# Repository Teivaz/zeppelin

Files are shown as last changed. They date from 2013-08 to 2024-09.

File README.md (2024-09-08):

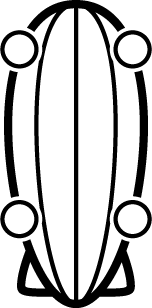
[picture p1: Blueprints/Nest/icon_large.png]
# Zeppelin 

### Airship project with all electrical circuits, PCBs, blueprints, software sources and calculations

### Intended result
First version of this zeppelin should be able to keep itself up in the sky for a decent amount of time. It will be controled remotely (probably via iphone). Total length of airship 168.13cm. Volume 0.46 m3.
In the end it should look like this:    
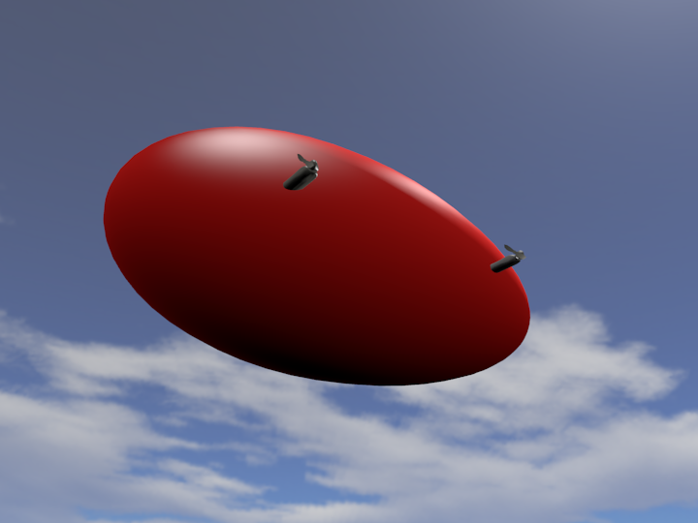
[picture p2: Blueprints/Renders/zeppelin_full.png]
zeppelin in all its glory


### Progress
 - [X] Calculate the overall size, mass, and lifting force of the aerostat
 - [X] Create patterns for aerostat
 - [X] Create electrical schemas
 - [X] Design software architecture
 - [ ] Create and debug airship's software
 - [ ] Create software for controlling unit
 - [ ] Trace PCBs and make all PCBs
 - [ ] Assemble aerostat
 - [ ] Field tests

### Calculations
Here is the [link](https://docs.google.com/spreadsheets/d/1KFVUaK0Eav1PAXg2VrwWtU-BHmDxbaWGcJfdvVmI2J4/edit?usp=sharing) to spreadsheet with calculation I made for the lifting force and mass of the airship 

### Mechanics
Most parts used here were thoroughly measured and calculated. Like these cases for motors and servos (feather module)   
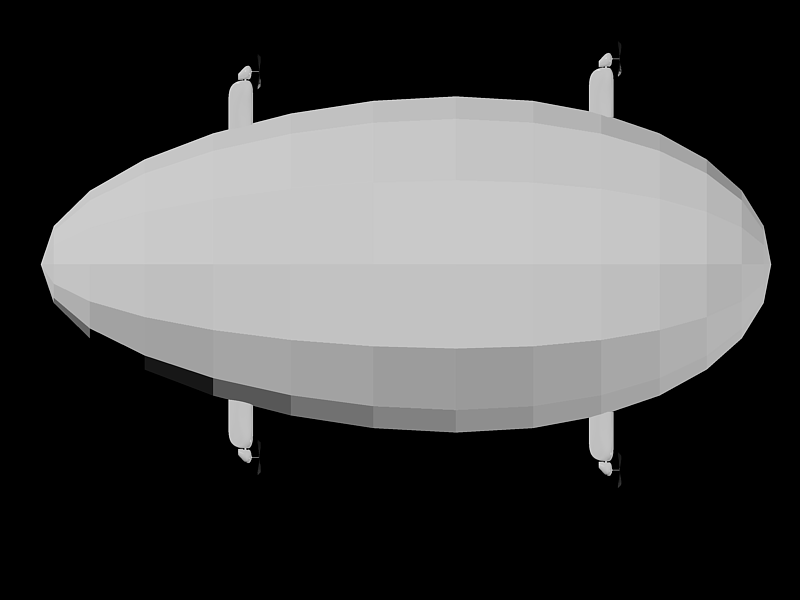
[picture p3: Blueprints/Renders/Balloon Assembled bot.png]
preview
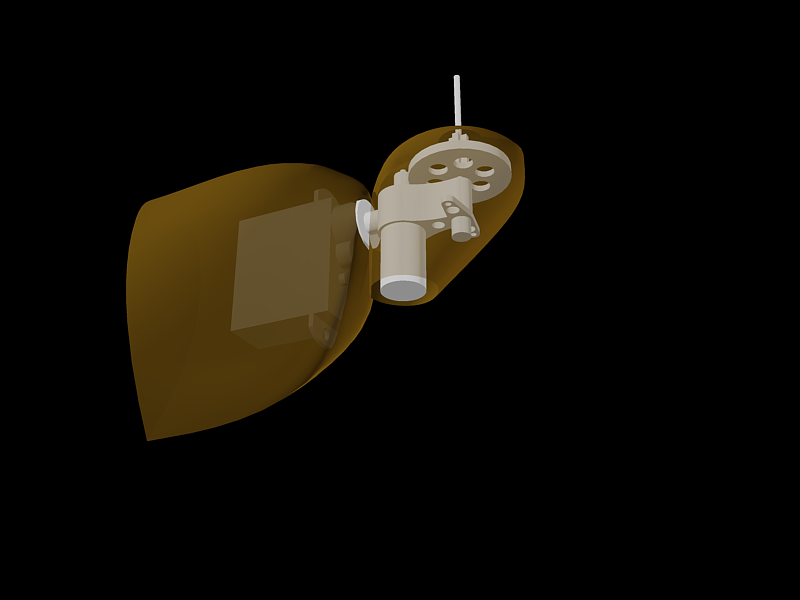
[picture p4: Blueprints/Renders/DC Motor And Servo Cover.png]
feather


### Electronic schematics and PCBs
Well there's not much to say about schematics despite the fact that I'm using ST microcontroller stm32l011f4 and transmitting modules nRF24013. It is designed and traced with [EAGLE](https://www.autodesk.com/products/eagle/overview).

### Software
I am using smt32l011 and the IDE is [VS Code](https://code.visualstudio.com). The language is C with HAL library.

### Version 1.0 considerations
 * Feather MCU should use internal PWM channels directly. This will simplify code and increase working frequency.
 * Feather should use a motor driver that does not short circuit when in low phase of the PWM.
 * Consider using 8 bit controller for the Feather module.

### Further plans
 * Second version will be able to carry a camera.
 * Third version will automatically keep position, folow the route or target.

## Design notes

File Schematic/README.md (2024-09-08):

# Change log

## Version 1.1
Status: In development
Changes:
 - [Keel] Added power regulator.
 - [Keel] Measuring Bat0 through divider.
 - [Feather] Changed pinout for PWM.

## Version 1.0.1
Status: Upgraded from v1.0.0
Changes:
 - [Keel] Replaced vertical connectors with horizontal (fixed connector pin numbers).
 - [Keel] Fixed LED polarity.
 - [Keel] Changed voltage divider resistor.
 - [Keel] Flipped the power switch.

## Version 1.0.0
Status: Manufactured

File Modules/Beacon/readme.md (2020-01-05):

# The Beacon module

This module is used only for testing purposes.

Every second the beacon tramsmits data that should be picked up by the device.

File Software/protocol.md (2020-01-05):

This document describes the communication protocol for the Zeppelin project.

Project URL: https://github.com/Teivaz/zeppelin
Author: Teivaz
Date: 4.01.2020
Version: 1.0

# Purpose
The communication protocol is used to for commands and data transmition between different parts of the Zeppelin.

# Adopting
This communication protocol is adopted by all parts of the system. Certain parts may not support all of the commands but the package structure should always be supported.

# Architecture
The protocol assumes single master and multiple slave devices.

# Package structure

```
|  Hdr  |  Adr  |  Len  |  RId  |  Cmd  |  Pld  |  CRC  |
|  0x55 |  1B   |  1B   |  1B   |  1B   |  ...  |  1B   |
```

The **Hdr** (Header) field. Size: 1 byte. The very first byte of every package starts with a **Hdr** field which is always `0x55` (`0b01010101`).
The **Adr** (Address) field. Size: 1 byte. Compatible with I2C 7 bit address. The MS bit is reserved and should always be 0.
The **Len** (Length) field. Size: 1 byte. Type: `uint8_t`. The length of the rest of the package including its **CRC** byte.
The **RId** (Request/Response Id) field. Size: 1 byte. Type: `uint8_t`. The unique id of the request that will be repeated by the response. Can be 0.
The **Cmd** (Command) of size 1 byte. Full list of commands is in the *Commands* section.
The **Pld** (Payload) field. Size: 0-26 bytes.
The **CRC** field. The (polynomial 0x07, initial value 0x00) CRC-8 value of the whole package (excluding this field).

# Version
The protocol version is `0bMMMMmmmm` - where `M` - major version bits, `m` - minor version bits).

# Commands
Current version of protocol: `0x10`

The commands' most significant bit indicates direction of the command. 0 - request, 1 - response.
*Note* Not all commands have responses.

- `0x00` - *info*. Check presence of the device. Payload length: 0.
- `0x80` - *info-re*. Response to the *info* command. Payload length: 2 bytes. Payload data: 1 byte - device type id; 1 byte - version of the protocol.
- `0x01` - *read-cv* - read configurable value. Payload length: 1 byte. Payload data: 1 byte - id of the configurable value.
- `0x81` - *read-cv-re* - response to the *read-cv* command. Payload length: 2 bytes. Payload data: 1 byte - id of the configurable value; 1 byte - the value.
- `0x02` - *write-cv*. Set a configurable value. Payload length: 2 bytes. Payload data: 1 byte - id of the configurable value (see the list of configurables values for a specific device); 1 byte - the value.
- `0x82` - reserved.
- `0x03` - *reset-cv* - reset configurable value to defaul state. Payload length: 1 byte. Payload data: 1 byte - id of the configurable value.
- `0x83` - reserved.
- `0x04` - *reset-all-cv* - reset all configurable values to defaul state. Payload length: 0.
- `0x84` - reserved.
- `0x05` - *read-dv* - read dynamic value. Payload length: 1 byte. Payload data: 1 byte - id of the dynamic value.
- `0x85` - *read-dv-re* - response to the *read-dv* command. Payload length: 2 bytes. Payload data: 1 byte - id of the ; 1 byte - the value.
- `0x06` - *write-dv* -  Set a dynamic value. Payload length: 2 bytes. Payload data: 1 byte - id of the dynamic value (see the list of dynamic values for a specific device); 1 byte - the value.
- `0x86` - reserved.
- `0x07` - *reset-dv* - reset the dynamic value of the device to default. Payload length: 1 byte - id of the dynamic value.
- `0x87` - reserved.
- `0x08` - *reset-all-dv* - reset all dynamic values of the device to default. Payload length: 0.
- `0x88` - reserved.

# Device descriptions

## Address
Every device needs to have a uniqie address. If there are more than one device with the same address the result is undefined.
The address can be in the range 0x08 - 0x7b.

## Configurable values
The configurable values are persisten memmory cells that are used by the device. Normally stored in EEPROM.

## Dynamic values
The opearating values of the device (e.g. temperature).

## Feather
Device Type Id: `0x01`.
The servo and DC motor controller.

### Configurable values:
- `0x00` - The address of the device. Type: `uint8_t`. Default: `0x10`.
- `0x10` - default value for DC motor on startup. Type: `int8_t`. Default: `0`.
- `0x11` - calibrating minimal value for DC motor. Type: `int8_t`. Default: `-127`.
- `0x12` - calibrating maximal value for DC motor. Type: `int8_t`. Default: `127`.
- `0x13` - calibrating zero value for DC motor. Type: `int8_t`. Default: `0`.
- `0x20` - default value for the servo on startup. Type: `unt8_t`. Default: `0`.
- `0x21` - calibrating minimal value for the servo. Type: `uint8_t`. Default: `0`.
- `0x22` - calibrating maximal value for the servo. Type: `uint8_t`. Default: `255`.

### Dynamic values:
- `0x00` - value of DC motor. Type: `uint8_t`. Defaults to value of `0x00` configurable value.
- `0x01` - DC motor calibrating mode. Type: `int8_t`. Values: `[0, 1]`. When calibrating mode set to `1` the dynamic value `0x00` is not normalized and represents actual value that will be applied to the motor driver. Once this value is changed the actual value of the `0x00` is recalculated according to the mode in order to keep the motor driver at the same value.
- `0x10` - value of servo. Type: `int8_t`. Defaults to value if `0x10` configurable value.
- `0x11` - servo calibrating mode. Type: `int8_t`. Values: `[0, 1]`. When calibrating mode set to `1` the dynamic value `0x10` is not normalized and represents actual value that will be applied to the driver.

## Keel
Device Type Id: `0x02`.
Base communication hub with additional functions.

### Configurable values:
- `0x00` - The address of the device. Type: `uint8_t`. Default: `0x10`.

### Dynamic values:
- `0x00` - value of the battery0. Type: `uint8_t`. Read only (resetting/writing to it has no effect).
- `0x01` - value of the battery1. Type: `uint8_t`. Read only (resetting/writing to it has no effect).
- `0x10` - value of the thermometer0. Type `uint8_t`. Read only (resetting/writing to it has no effect).

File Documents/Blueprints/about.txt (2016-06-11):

Maximal radius 38.7 cm
Total length 168.13 cm
Arc length 198.9 cm
Volume 490047.55 cm3
Square 33496 cm2
Mass centrum from bow 79.48 cm

Mass:
Servos 4.4 g
Screw 1 g
Accumulator 1.1 - 28.2 g
Accumulator 0.1 - 4.8 g
Motors - 3.5 g
Transciever - 2 g

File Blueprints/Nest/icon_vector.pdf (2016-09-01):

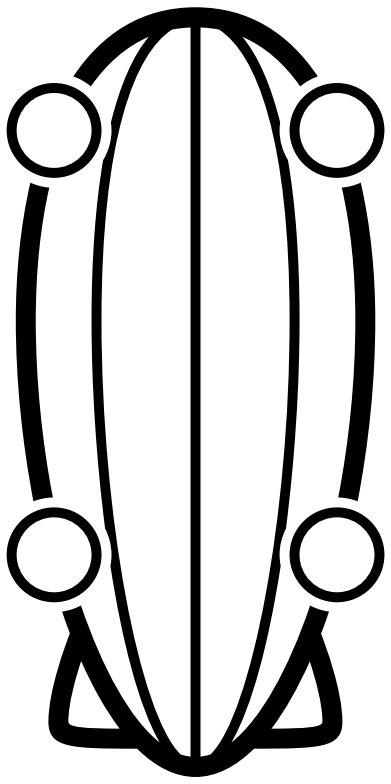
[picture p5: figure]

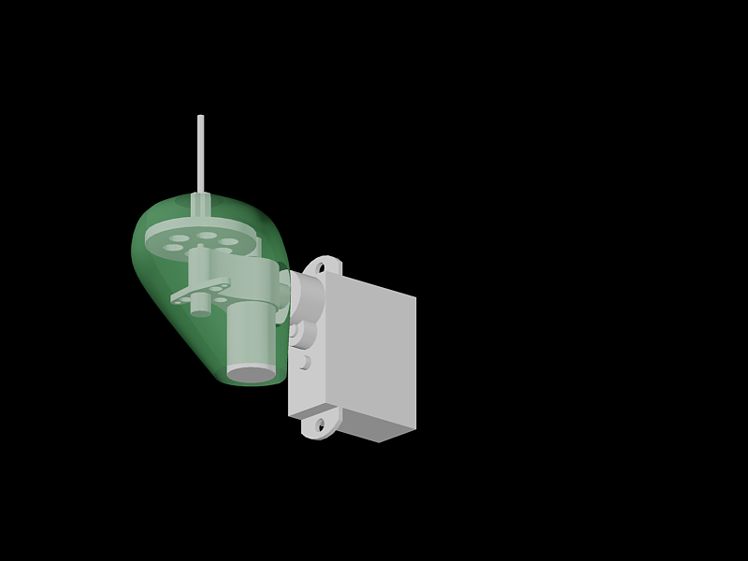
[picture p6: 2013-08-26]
Blueprints/Renders/DC Motor Cover.png

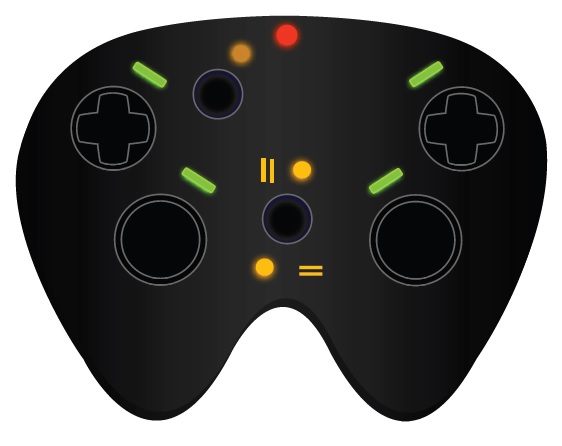
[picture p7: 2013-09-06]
Blueprints/Renders/Nest Prototype.jpg

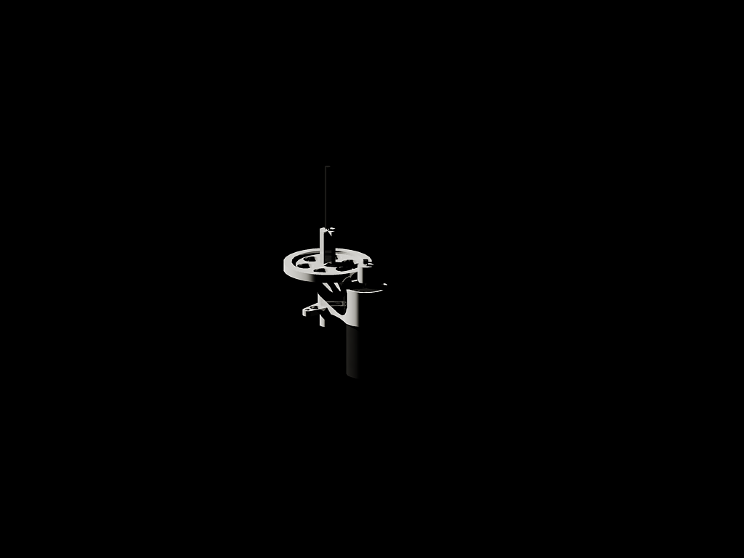
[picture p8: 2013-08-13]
Blueprints/Renders/DC Motor.png

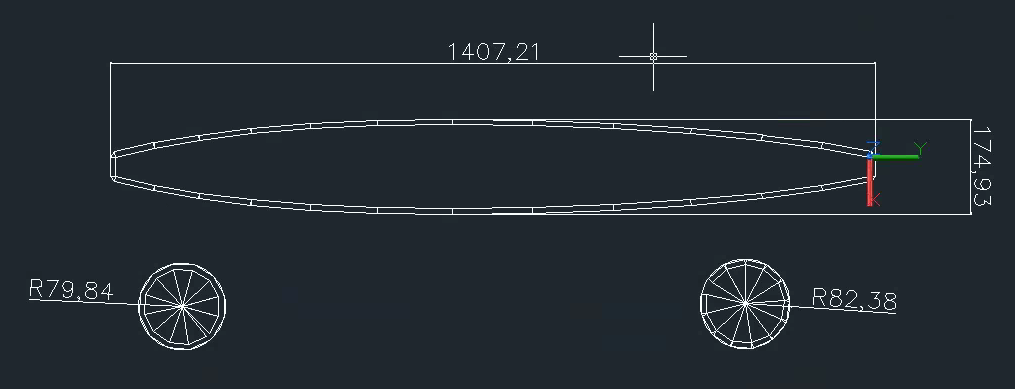
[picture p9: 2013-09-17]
Blueprints/balloon segment dimensions.png

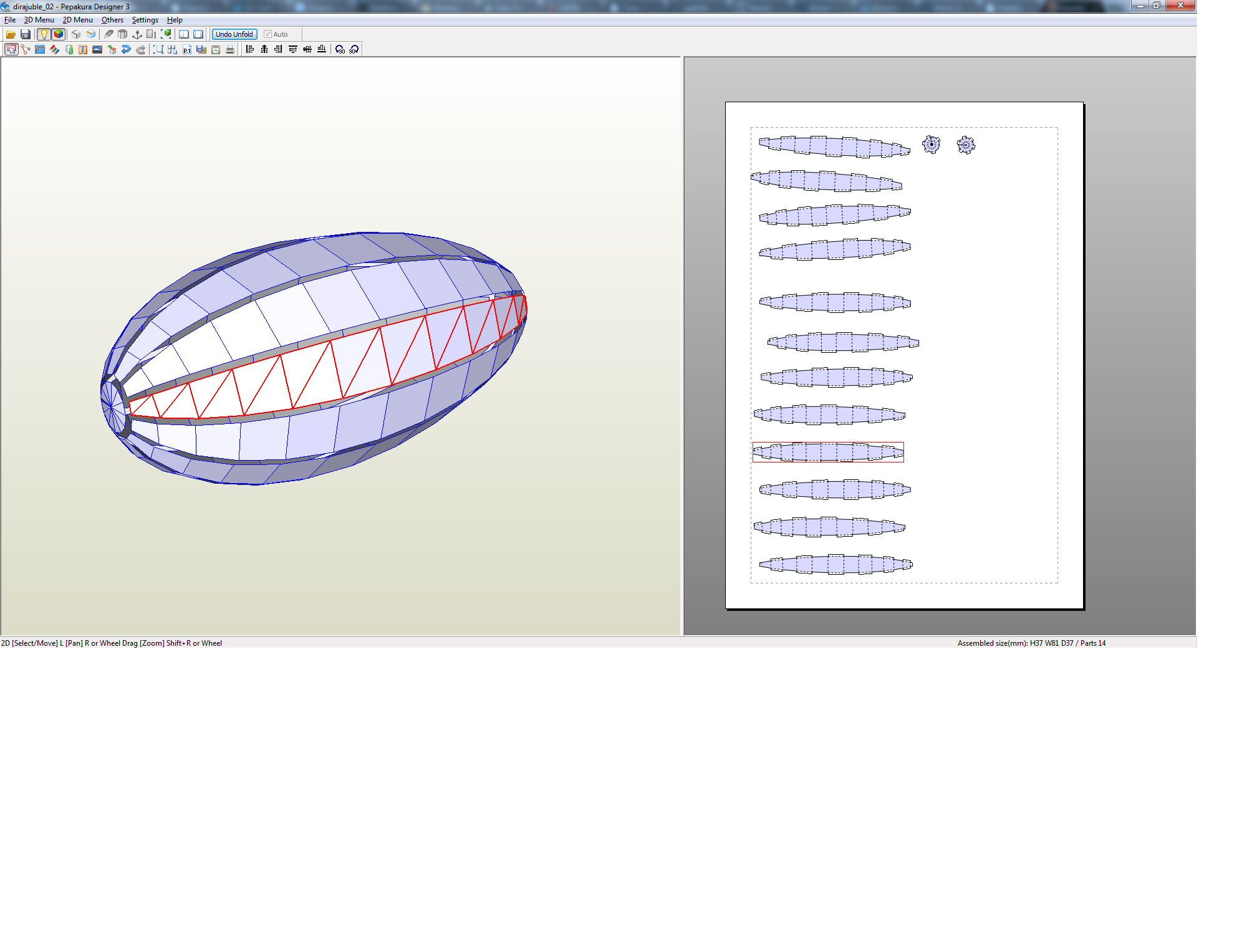
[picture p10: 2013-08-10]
Documents/Blueprints/model1.png

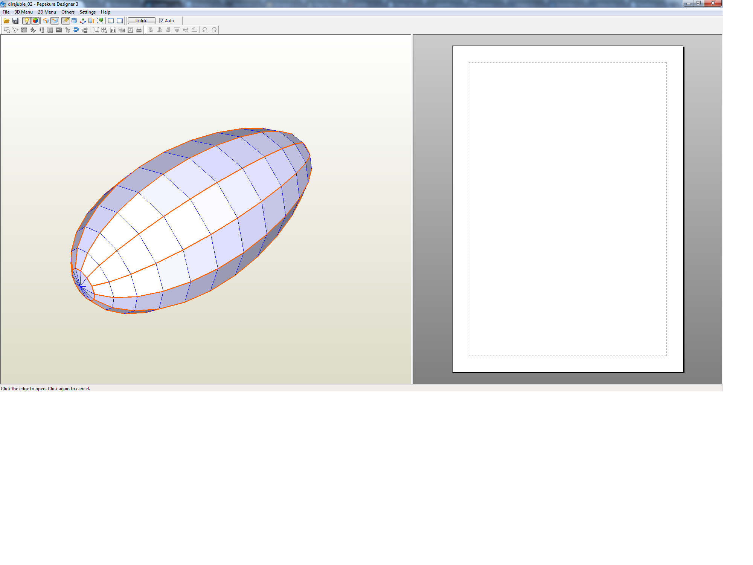
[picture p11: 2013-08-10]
Documents/Blueprints/model.png

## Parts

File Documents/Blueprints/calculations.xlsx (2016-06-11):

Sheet: General
Item | Mass | Number | Total mass
Aerostat | 405.3016 | 1 | 405.3016
Servos | 4.4 | 4 | 17.6
Screw | 1 | 4 | 4
Accumulator 1.1 Ah | 28.2 | 1 | 28.2
Accumulator 0.1 Ah | 4.8 | 1 | 4.8
Motor | 3.5 | 4 | 14
Transciever | 2 | 1 | 2
Wires | 10 | 1 | 10 | ?
Mounts | 5 | 4 | 20 | ?
Electronics | 15 | 1 | 15 | ?
Airship weight |  |  | 520.9016 | g
Aerostat liftig force |  |  | 782.7039469 | g
Remaining lifting force |  |  | 261.8023469 | g

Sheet: Balloon
 | cm | m |  | m
Arc Length | 198.9 | 1.989 |  | 2.1879
Maximal circumference | 243.036 | 2.43036 |  | 2.673396
Maximal radius | 38.7 | 0.387 |  | 0.4257
Length | 168.13 | 1.6813 |  | 1.84943
Mass centrum from bow | 76.48 | 0.7648 |  | 0.84128
 | cm2 | m2 |  | m2
Surface square | 33496 | 3.3496 |  | 4.053016
 | cm3 | m3 |  | m3
Volume | 490047.55 | 0.49004755 |  | 0.6522532891
Scale |  |  |  | 9.09E-01 | 1.1
 |  | kg
Liftig force |  | 0.58805706 |  | 0.7827039469
Material thickness | 1000000 | mkm |  | 1 | m |  | polyethylene | 0.94 | 50-60
Material density | 0.0001 | g/cm3 |  | 100 | g/m3 |  | polypropylene | 0.91
 |  |  |  |  |  |  | PVC | 1.35
Aerostat mass |  | 334.96 | g | 405.3016 | g
 |  |  |  |  |  |  | waterproof cloth | 150 | х1
 |  |  |  |  |  |  | special cool cloth I have | 100
 |  |  |  | 261.80
Выкройка
Размеры | 1407.21 | 174.93 | 79.84 | 82.38
Масштаб | 1.394073007
Итоговый размер | 1961.753477 | 243.8651912 | 111.3027889 | 114.8437343
Площадь ткани | 1961.753477 | 2926.382294 | м |  | 5.74084064 | м2

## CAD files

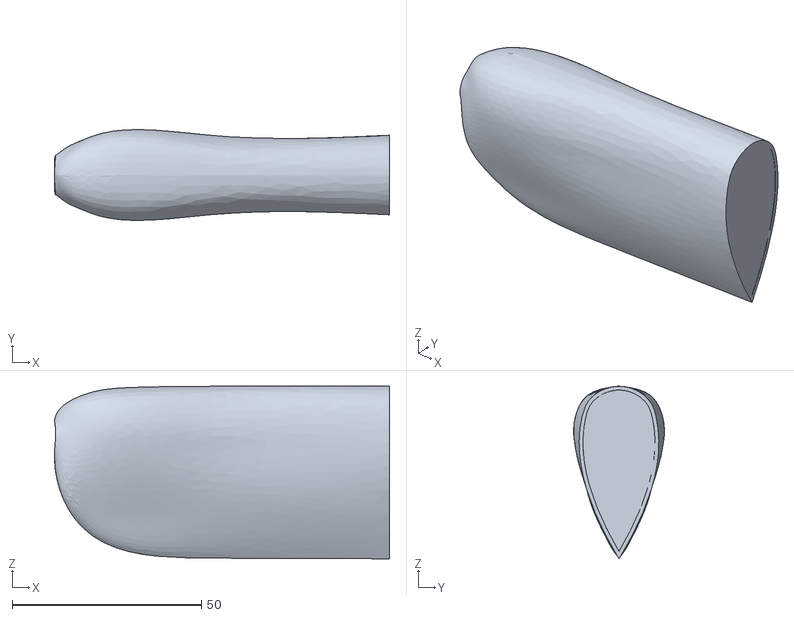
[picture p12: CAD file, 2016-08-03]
Blueprints/parts/feather_servo_cover.stl
88.5 x 24.0 x 45.6

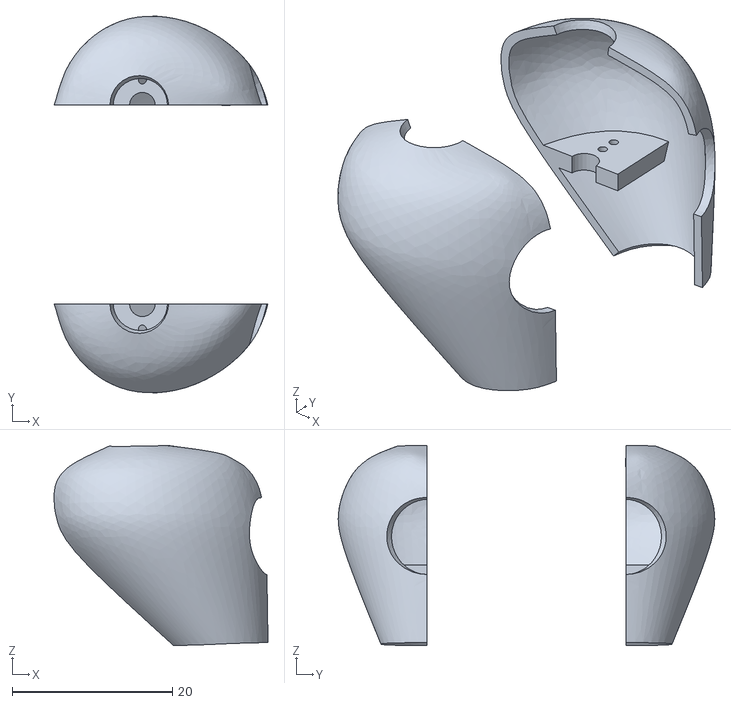
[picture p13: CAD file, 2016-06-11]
Outfiles/Blueprints/Feather_cover_print.stl
26.7 x 47.0 x 25.0

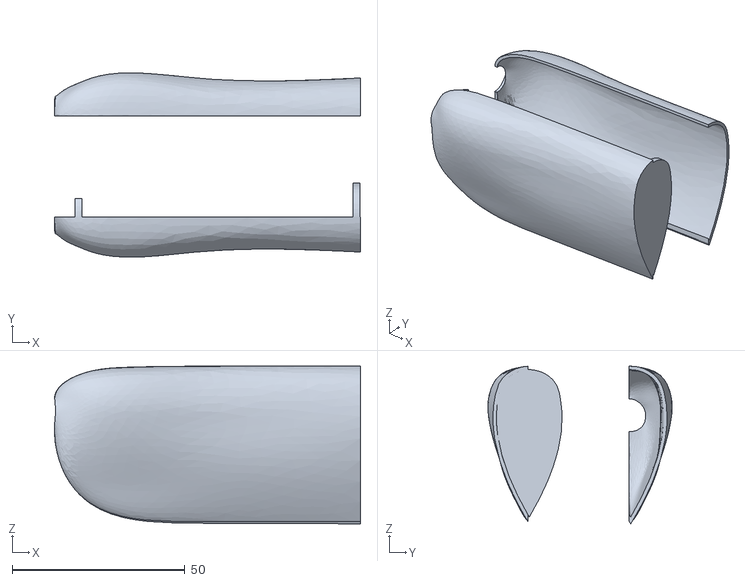
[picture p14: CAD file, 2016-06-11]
Outfiles/Blueprints/Feather_cover2_print.stl
88.5 x 53.3 x 45.6

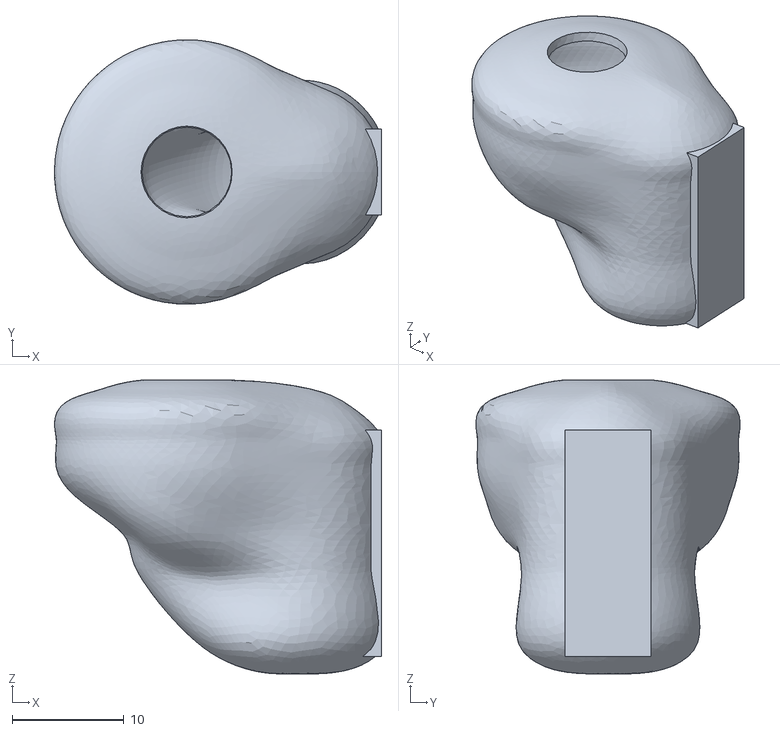
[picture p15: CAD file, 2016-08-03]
Blueprints/parts/feather_motor_cover.stl
29.3 x 23.7 x 26.3

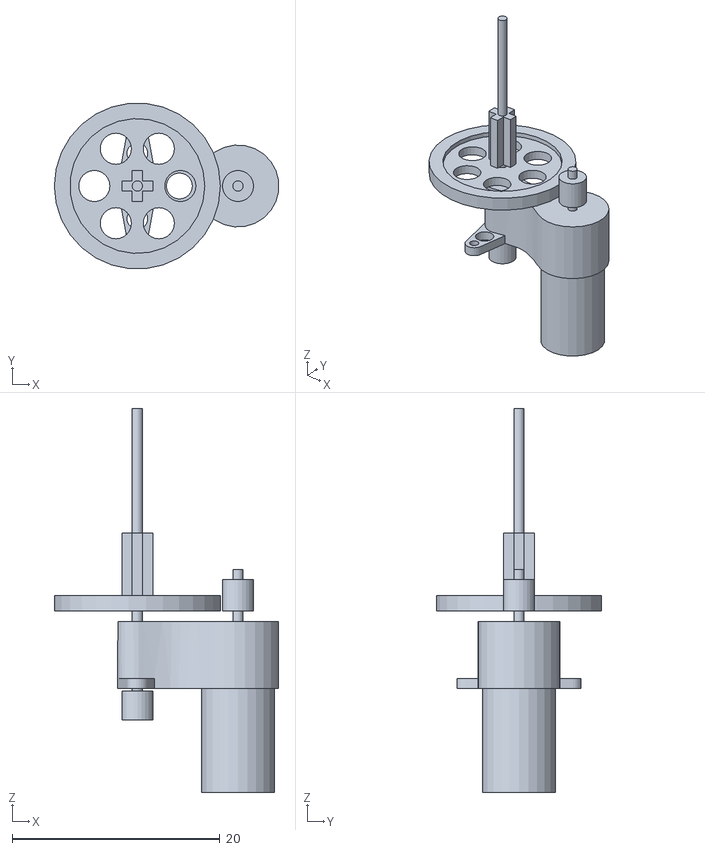
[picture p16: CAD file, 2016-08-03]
Blueprints/parts/feather_motor.stl
21.6 x 15.9 x 37.0

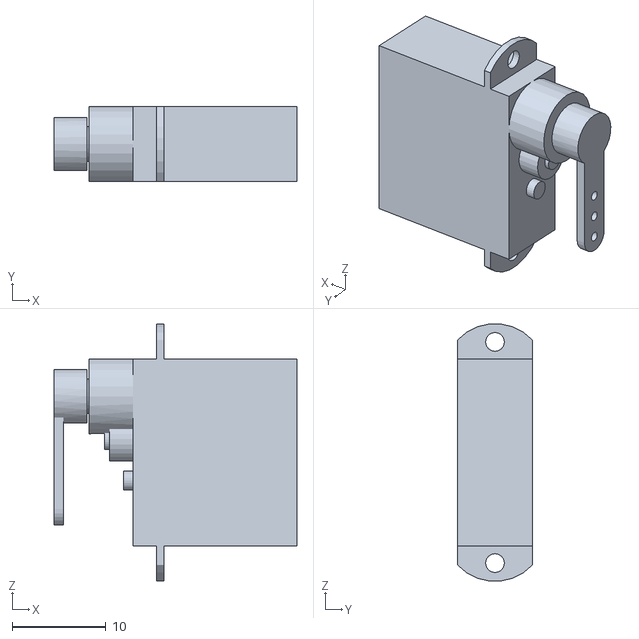
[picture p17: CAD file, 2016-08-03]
Blueprints/parts/feather_servo.stl
25.9 x 8.00 x 27.4

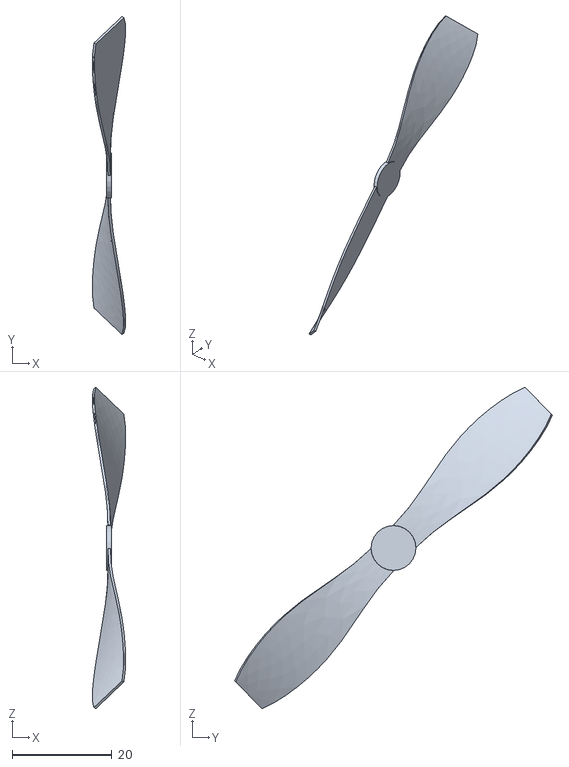
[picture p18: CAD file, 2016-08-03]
Blueprints/parts/feather_screw.stl
6.70 x 63.8 x 64.5

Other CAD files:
Blueprints/Feather.dwg
Blueprints/Nest/stick.dwg
Blueprints/Nest/Protype.dwg
Blueprints/wrap.dwg
Blueprints/baloon.dwg
Blueprints/Nest/stick3d.dwg
Blueprints/Nest/mode_icons.dwg
Blueprints/parts.dwg
Blueprints/Renders/assembled_balloon.blend

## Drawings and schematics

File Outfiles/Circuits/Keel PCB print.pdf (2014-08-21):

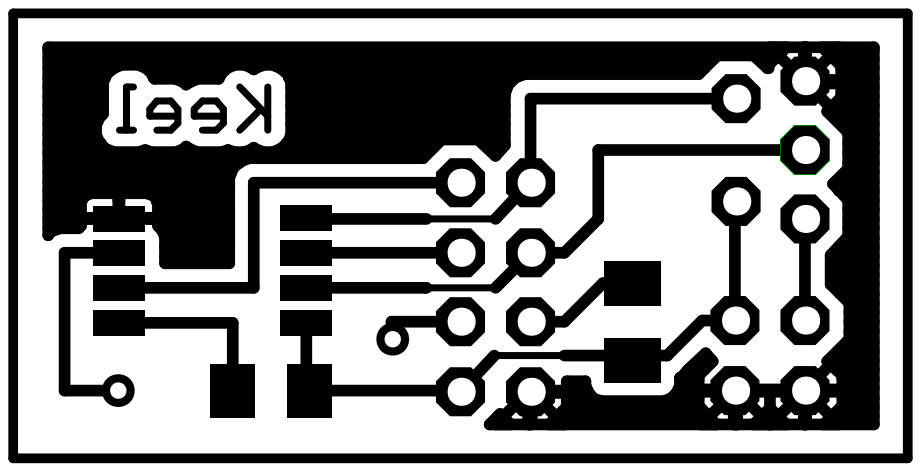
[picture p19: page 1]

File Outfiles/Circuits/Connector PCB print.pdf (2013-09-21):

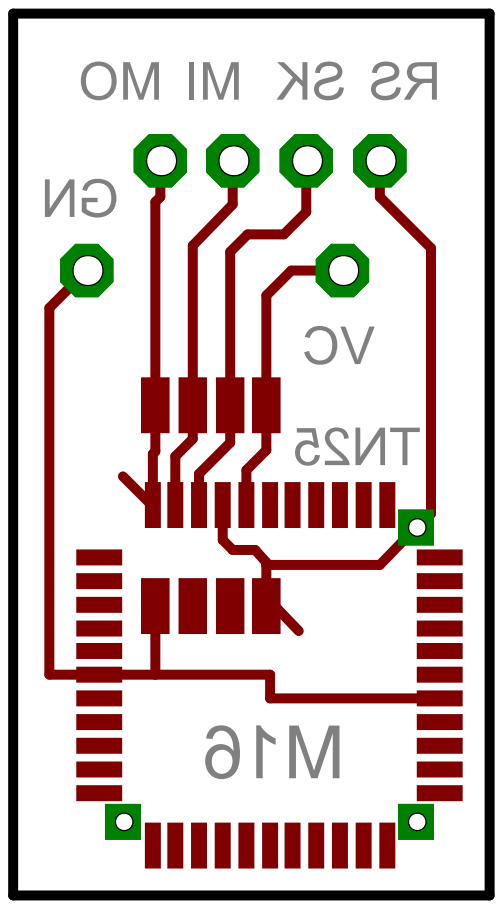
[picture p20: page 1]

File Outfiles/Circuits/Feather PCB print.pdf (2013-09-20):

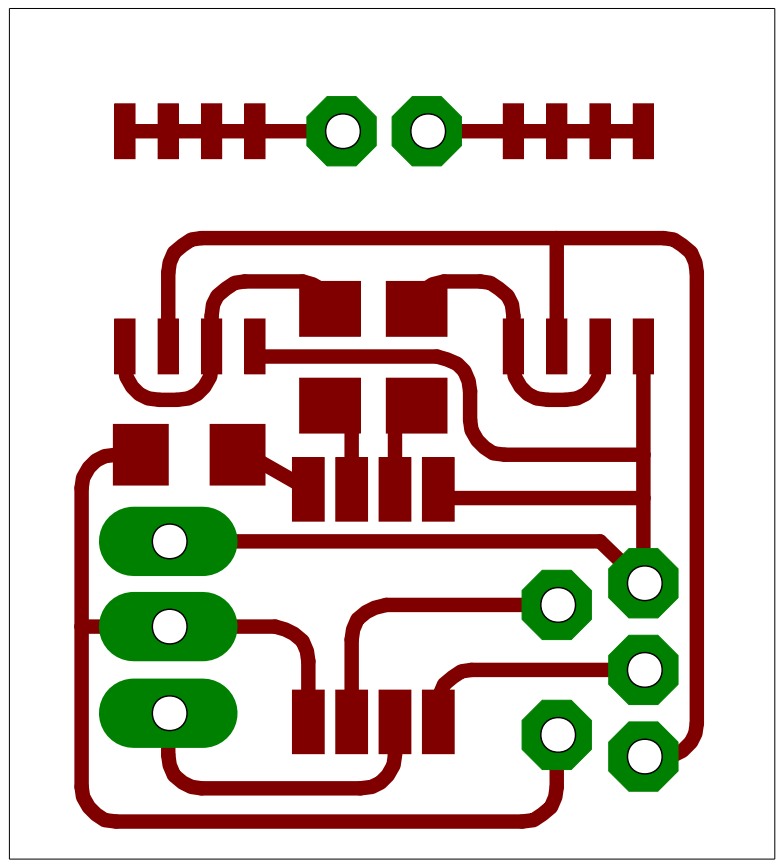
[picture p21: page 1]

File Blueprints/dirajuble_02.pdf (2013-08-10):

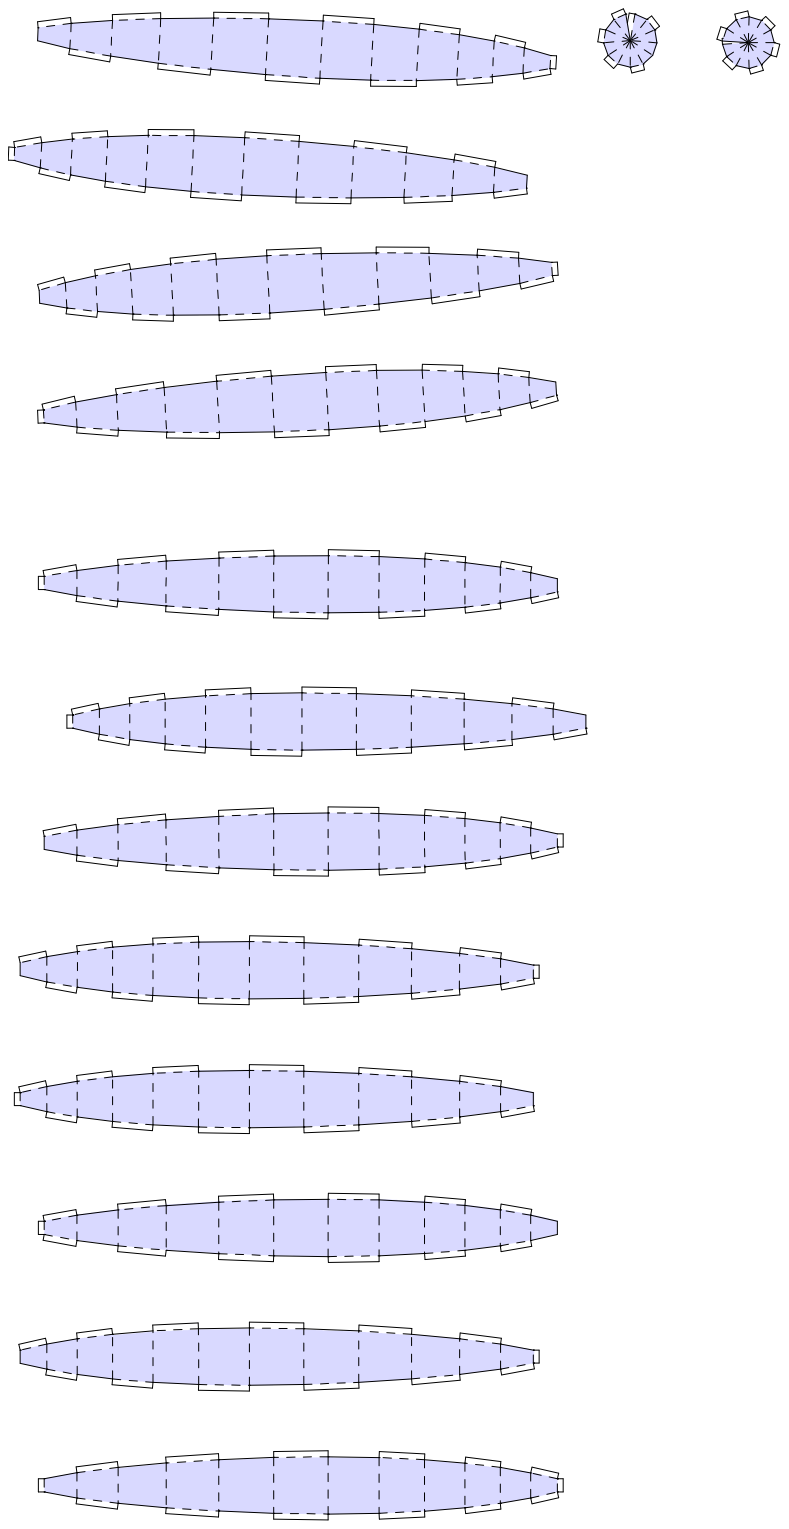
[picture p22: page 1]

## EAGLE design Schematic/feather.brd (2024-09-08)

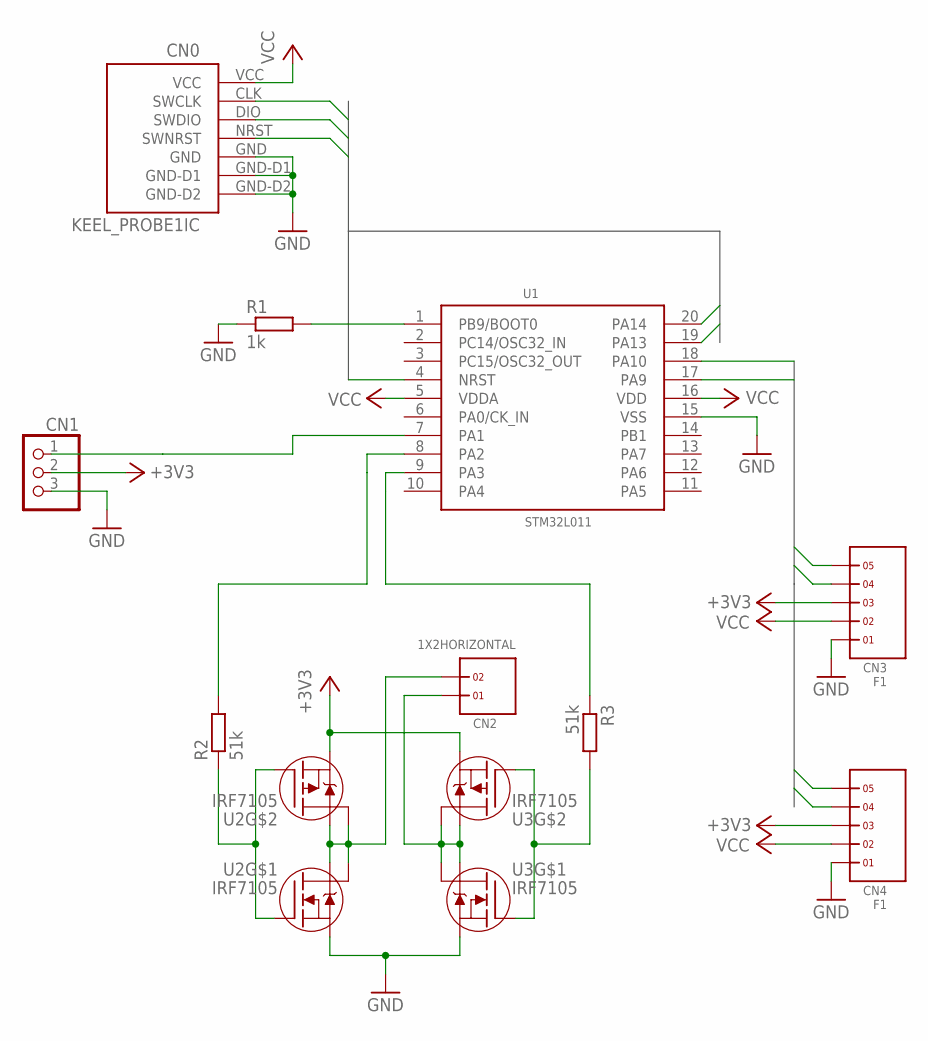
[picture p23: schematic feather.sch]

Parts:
CN0: KEEL_PROBE1IC; KEEL_PROBE-IC1
CN1: PINHD-1X3/90; 1X03/90
CN2: 1X2HORIZONTAL; 1X2H
CN3, CN4: F1; 1X5H
R1: 1k; R0805
R2, R3: 51k; R0805
U1: STM32L011; SSOP20
U2, U3: IRF7105; SO8-2

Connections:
+3V3: CN1.2, CN3.3, CN4.3, U2.3 (S), U3.3 (S)
GND: CN0.GND, CN0.GND-D1, CN0.GND-D2, CN1.3, CN3.1, CN4.1, R1.1, U1.15 (VSS), U2.1 (S), U3.1 (S)
I2C_SCL: CN3.4, CN4.4, U1.17 (PA9)
I2C_SDA: CN3.5, CN4.5, U1.18 (PA10)
unnamed: CN2.2, U2.5 (D), U2.6 (D), U2.7 (D), U2.8 (D)
unnamed: R3.1, U1.9 (PA3)
unnamed: R3.2, U3.2 (G), U3.4 (G)
unnamed: CN2.1, U3.5 (D), U3.6 (D), U3.7 (D), U3.8 (D)
unnamed: R2.2, U1.8 (PA2)
unnamed: R2.1, U2.2 (G), U2.4 (G)
unnamed: R1.2, U1.1 (PB9/BOOT0)
unnamed: CN1.1, U1.7 (PA1)
NRST: CN0.NRST (SWNRST), U1.4 (NRST)
SWCLK: CN0.CLK (SWCLK), U1.20 (PA14)
SWDIO: CN0.DIO (SWDIO), U1.19 (PA13)
VCC: CN0.VCC, CN3.2, CN4.2, U1.5 (VDDA), U1.16 (VDD)

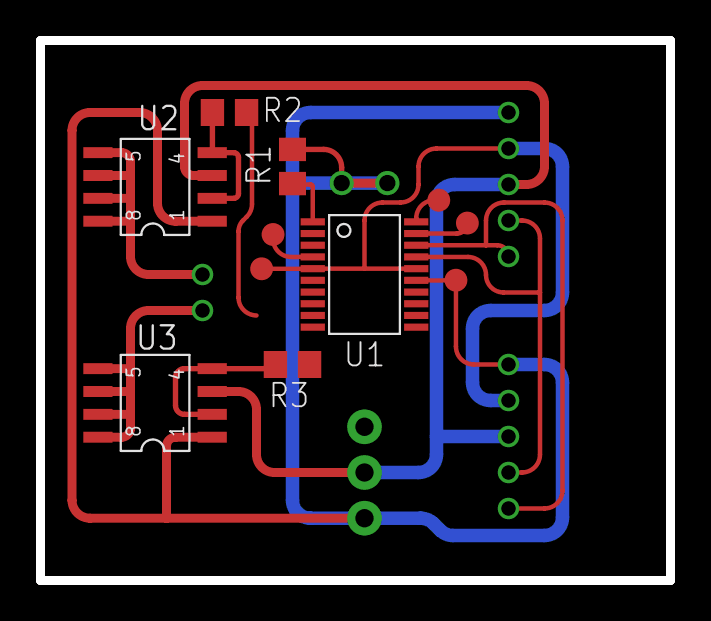
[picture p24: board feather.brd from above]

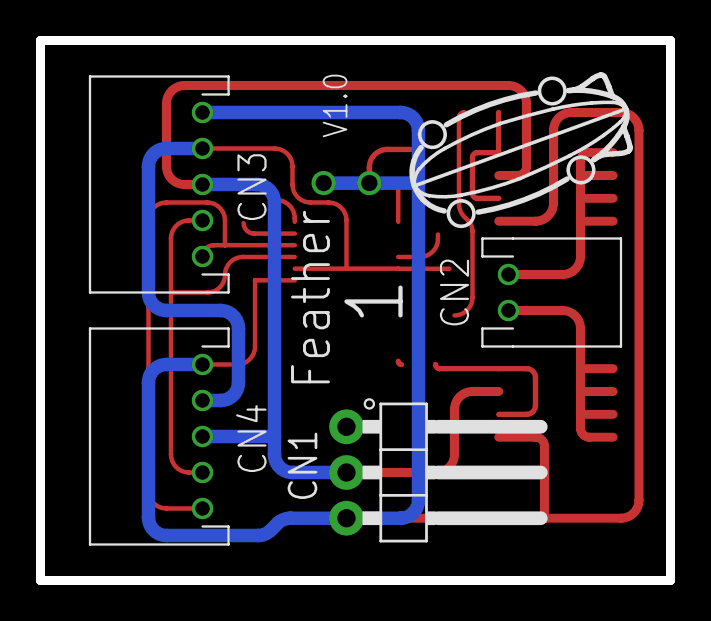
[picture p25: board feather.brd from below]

Board: 2 copper layers, 35.0 x 30.0 mm, 12 parts (5 on the bottom side), 16 nets.

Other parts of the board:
E$5: ZEPPELIN

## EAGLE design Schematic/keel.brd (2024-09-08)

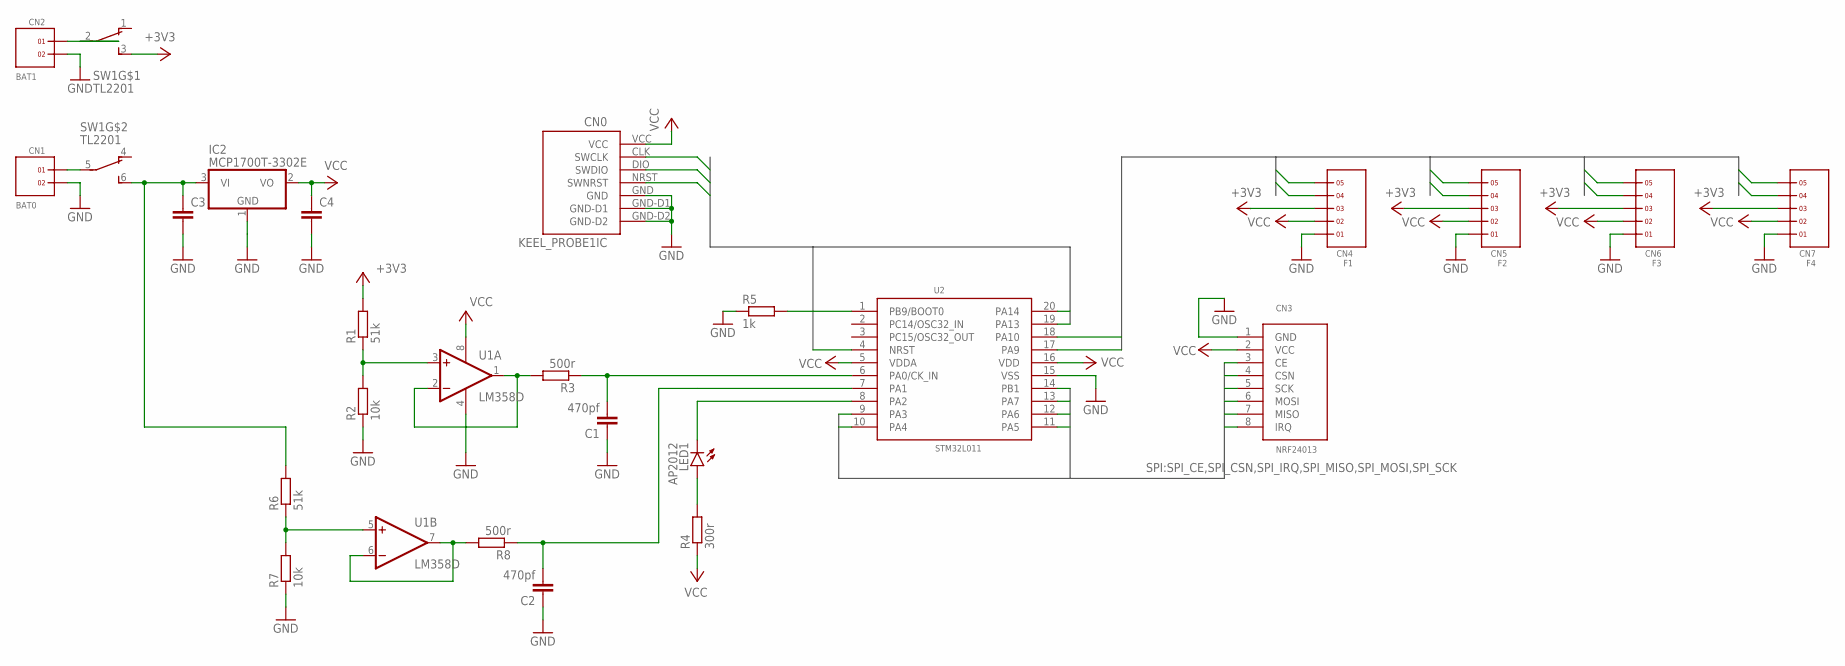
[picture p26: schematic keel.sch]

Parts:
C1, C2: 470pf; C0805
C3, C4: C-EUC0805; C0805
CN0: KEEL_PROBE1IC; KEEL_PROBE-IC1
CN1: BAT0; 1X2
CN2: BAT1; 1X2
CN3: NRF24013; PIN
CN4: F1; 1X5H
CN5: F2; 1X5H
CN6: F3; 1X5H
CN7: F4; 1X5H
IC2: MCP1700T-3302E; SOT23
LED1: AP2012
R1, R6: 51k; R0805
R2, R7: 10k; R0805
R3, R8: 500r; R0805
R4: 300r; R0805
R5: 1k; R0805
SW1: TL2201
U1: LM358D; SO08
U2: STM32L011; SSOP20

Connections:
+3V3: CN4.3, CN5.3, CN6.3, CN7.3, R1.2, SW1.3
GND: C1.1, C2.1, C3.2, C4.2, CN0.GND, CN0.GND-D1, CN0.GND-D2, CN1.2, CN2.2, CN3.1 (GND), CN4.1, CN5.1, CN6.1, CN7.1, IC2.1 (GND), R2.1, R5.1, R7.1, U1.4 (V-), U2.15 (VSS)
I2C_SCL: CN4.4, CN5.4, CN6.4, CN7.4, U2.17 (PA9)
I2C_SDA: CN4.5, CN5.5, CN6.5, CN7.5, U2.18 (PA10)
unnamed: R1.1, R2.2, U1.3 (+IN)
unnamed: LED1.C, U2.8 (PA2)
unnamed: LED1.A, R4.2
unnamed: C1.2, R3.1, U2.6 (PA0/CK_IN)
unnamed: R5.2, U2.1 (PB9/BOOT0)
unnamed: R3.2, U1.1 (OUT), U1.2 (-IN)
unnamed: CN2.1, SW1.2
unnamed: CN1.1, SW1.5 (2)
unnamed: R8.2, U1.6 (-IN), U1.7 (OUT)
unnamed: R6.1, R7.2, U1.5 (+IN)
unnamed: C2.2, R8.1, U2.7 (PA1)
unnamed: C3.1, IC2.3 (VI), R6.2, SW1.6 (3)
NRST: CN0.NRST (SWNRST), U2.4 (NRST)
SPI_CE: CN3.3 (CE), U2.10 (PA4)
SPI_CSN: CN3.4 (CSN), U2.9 (PA3)
SPI_IRQ: CN3.8 (IRQ), U2.14 (PB1)
SPI_MISO: CN3.7 (MISO), U2.12 (PA6)
SPI_MOSI: CN3.6 (MOSI), U2.13 (PA7)
SPI_SCK: CN3.5 (SCK), U2.11 (PA5)
SWCLK: CN0.CLK (SWCLK), U2.20 (PA14)
SWDIO: CN0.DIO (SWDIO), U2.19 (PA13)
VCC: C4.1, CN0.VCC, CN3.2 (VCC), CN4.2, CN5.2, CN6.2, CN7.2, IC2.2 (VO), R4.1, U1.8 (V+), U2.5 (VDDA), U2.16 (VDD)

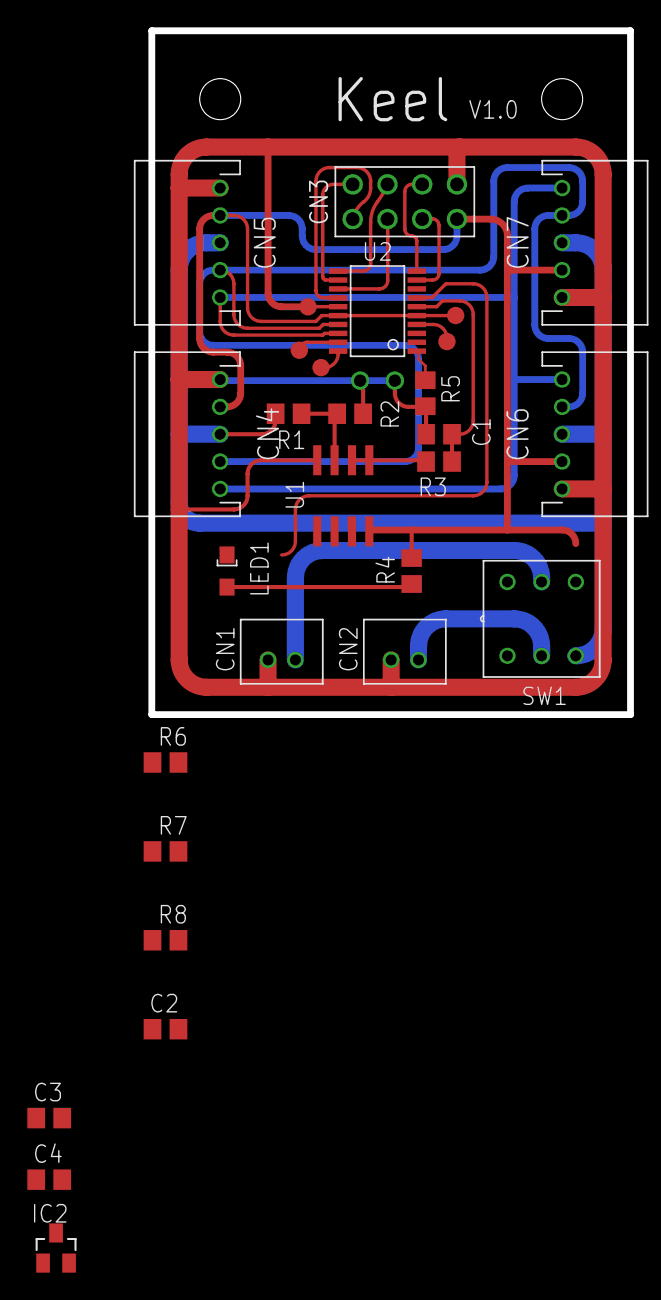
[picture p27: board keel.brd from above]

Board: 2 copper layers, 35.0 x 50.0 mm, 26 parts (1 on the bottom side), 26 nets.

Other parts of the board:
E$5: ZEPPELIN

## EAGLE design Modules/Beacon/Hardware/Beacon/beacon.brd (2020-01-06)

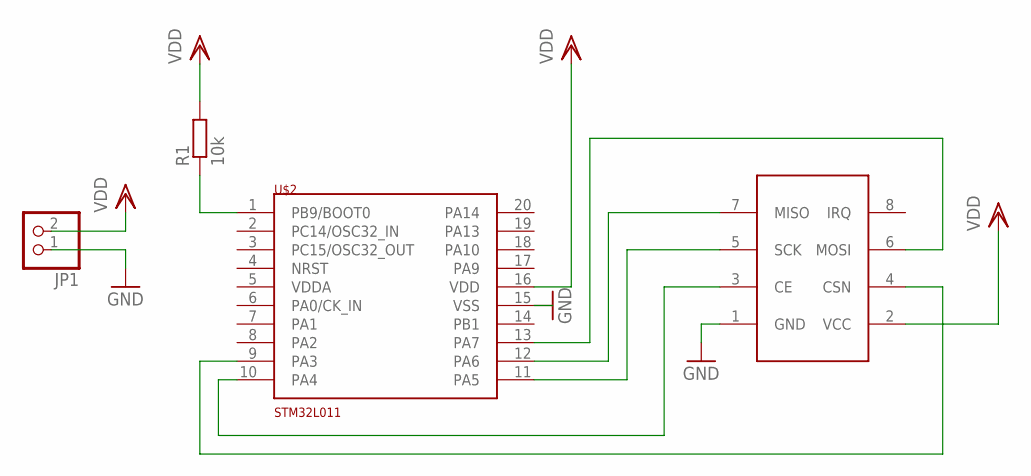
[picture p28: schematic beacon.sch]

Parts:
JP1: PINHD-1X2; 1X02
R1: 10k; R0805
U$1: RF24013; PIN
U$2: STM32L011; SSOP20

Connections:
CE: U$1.3 (CE), U$2.10 (PA4)
CSN: U$1.4 (CSN), U$2.9 (PA3)
GND: JP1.1, U$1.1 (GND), U$2.15 (VSS)
MISO: U$1.7 (MISO), U$2.12 (PA6)
MOSI: U$1.6 (MOSI), U$2.13 (PA7)
unnamed: R1.1, U$2.1 (PB9/BOOT0)
SCK: U$1.5 (SCK), U$2.11 (PA5)
VDD: JP1.2, R1.2, U$1.2 (VCC), U$2.16 (VDD)
VDDA: U$2.5 (VDDA)

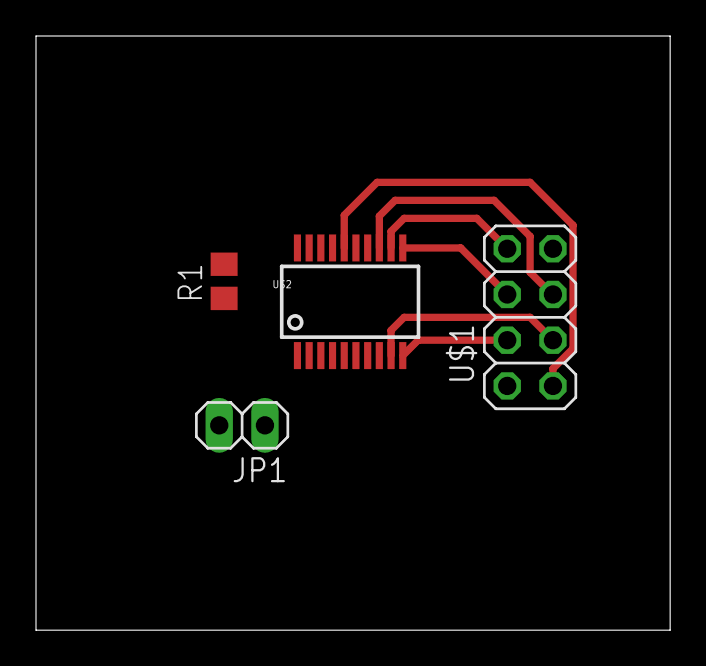
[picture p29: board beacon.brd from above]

Board: 2 copper layers, 35.2 x 33.0 mm, 4 parts (0 on the bottom side), 8 nets.

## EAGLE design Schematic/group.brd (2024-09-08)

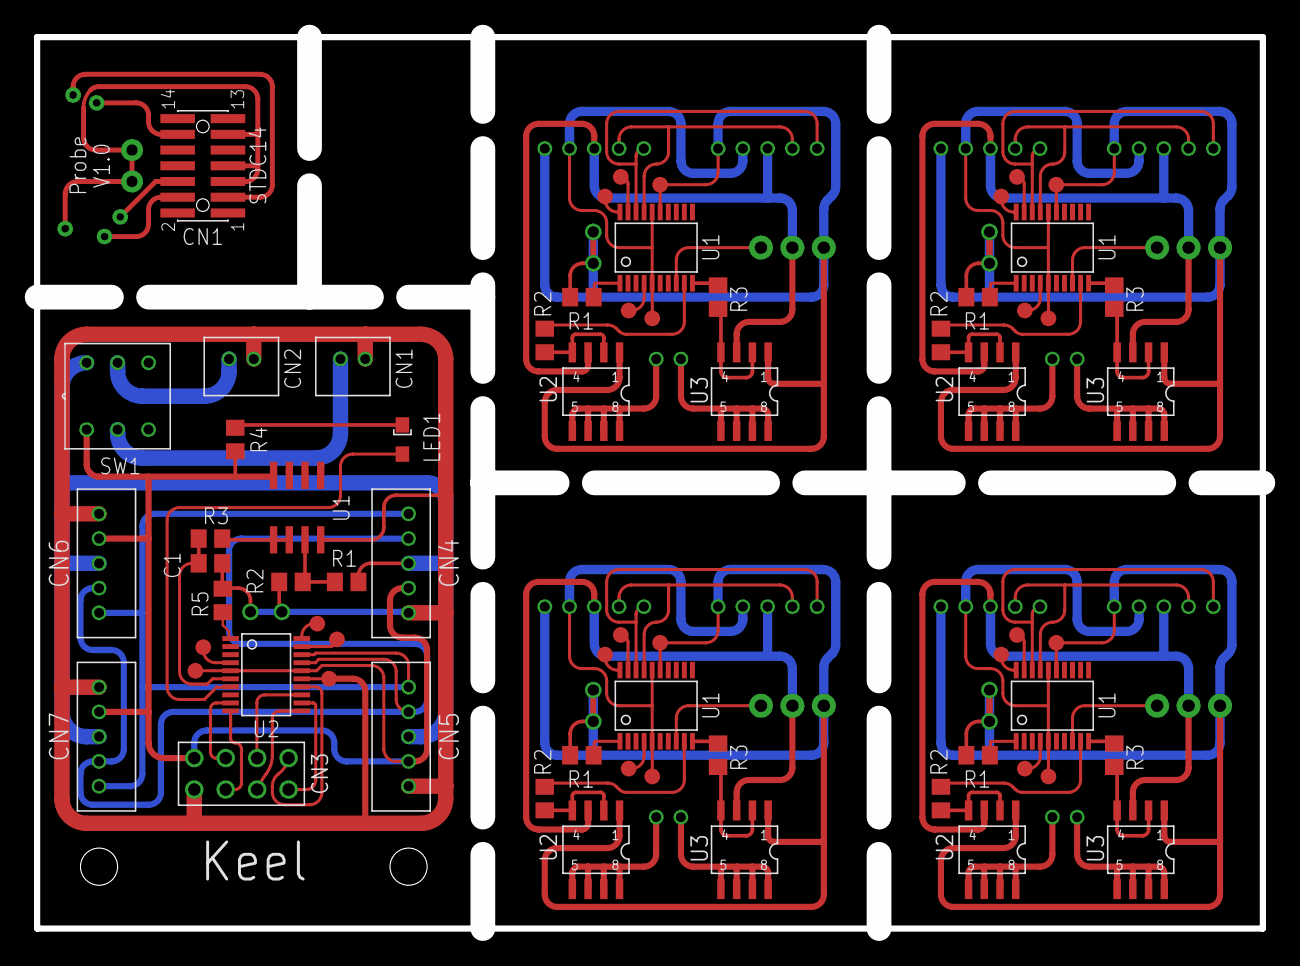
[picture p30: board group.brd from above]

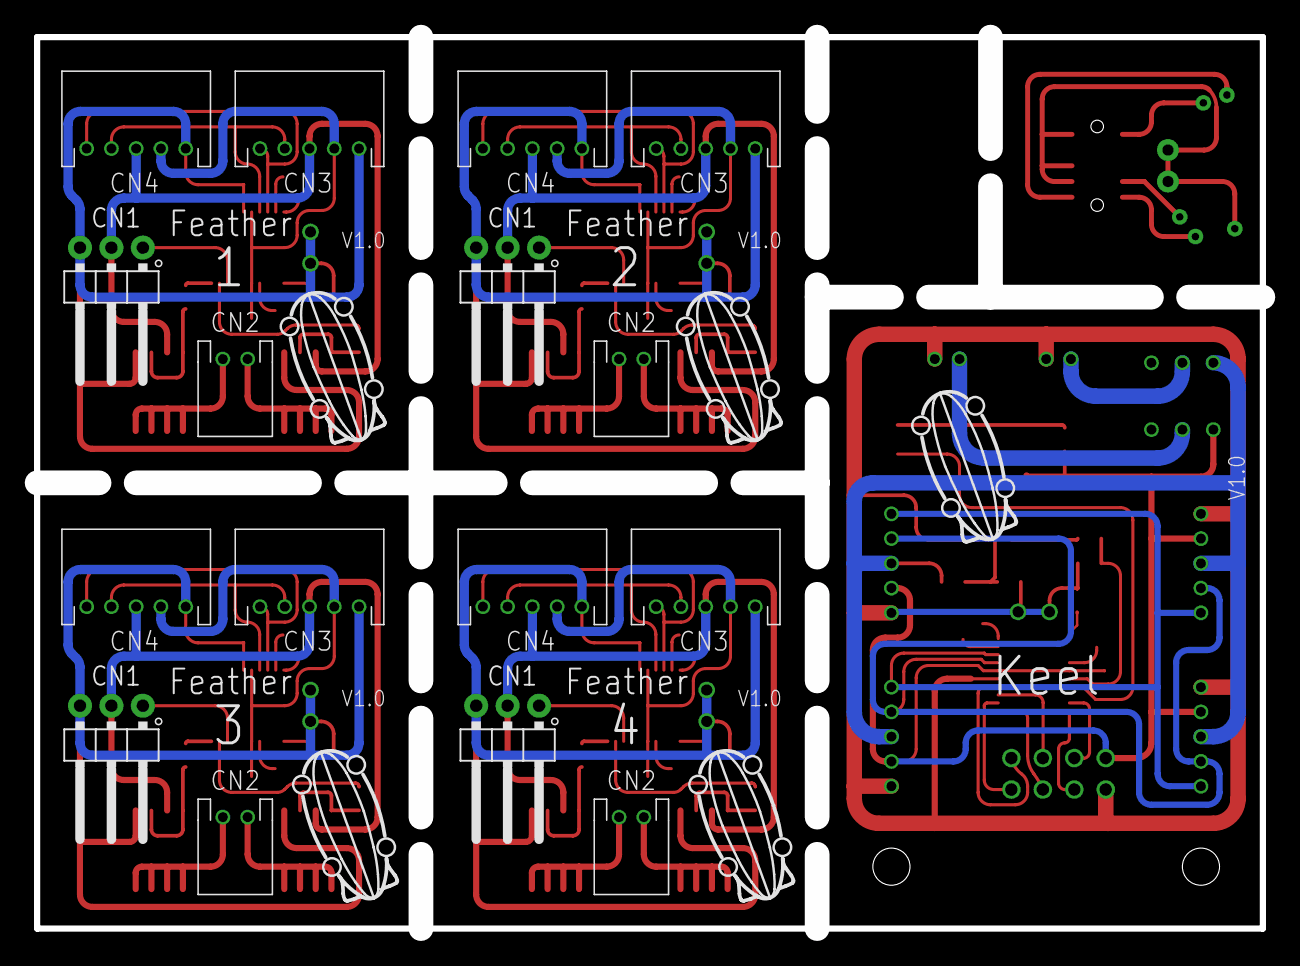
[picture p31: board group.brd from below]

Board: 2 copper layers, 99.0 x 72.0 mm, 69 parts (21 on the bottom side), 91 nets.

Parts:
C1: 470pf; C0805
CN0, CN10, CN15, CN20, CN25: KEEL_PROBE1IC; KEEL_PROBE-IC1
CN1: STDC14; FTSH-107-01-L-DV-K-A
CN2: KEEL_PROBE1PROBE; KEEL_PROBE1
CN3: BAT0; 1X2
CN4: BAT1; 1X2
CN5: NRF24013; PIN
CN6: F1; 1X5
CN7: F2; 1X5
CN8: F3; 1X5
CN9: F4; 1X5
CN11, CN16, CN21, CN26: 1X2HORIZONTAL; 1X2H
CN12, CN14, CN17, CN19, CN22, CN24, CN27, CN29: F1; 1X5H
CN13, CN18, CN23, CN28: 1X03/90
E$1, E$2, E$3, E$4, E$5: ZEPPELIN
LED1: AP2012
R1, R2: 10k; R0805
R3: 500r; R0805
R4: 300r; R0805
R5, R8, R11, R14, R17: 1k; R0805
R6, R7, R9, R10, R12, R13, R15, R16: 51k; R0805
SW1: TL2201
U1: LM358D; SO08
U2, U5, U8, U11, U14: STM32L011; SSOP20
U3, U4, U6, U7, U9, U10, U12, U13: IRF7105; SO8-2

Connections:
+3V1: CN12.3, CN13.2, CN14.3, U3.3, U4.3
+3V2: CN17.3, CN18.2, CN19.3, U6.3, U7.3
+3V3: CN6.3, CN7.3, CN8.3, CN9.3, R1.2, SW1.4
+3V4: CN22.3, CN23.2, CN24.3, U9.3, U10.3
+3V5: CN27.3, CN28.2, CN29.3, U12.3, U13.3
GND: CN1.05, CN1.07, CN1.11, CN2.GND, CN2.GND-D1, CN2.GND-D2
GND1: C1.1, CN0.GND, CN0.GND-D1, CN0.GND-D2, CN3.2, CN4.2, CN5.1, CN6.1, CN7.1, CN8.1, CN9.1, R2.1, R5.1, U1.4, U2.15
GND2: CN10.GND, CN10.GND-D1, CN10.GND-D2, CN12.1, CN13.3, CN14.1, R8.1, U3.1, U4.1, U5.15
GND3: CN15.GND, CN15.GND-D1, CN15.GND-D2, CN17.1, CN18.3, CN19.1, R11.1, U6.1, U7.1, U8.15
GND4: CN20.GND, CN20.GND-D1, CN20.GND-D2, CN22.1, CN23.3, CN24.1, R14.1, U9.1, U10.1, U11.15
GND5: CN25.GND, CN25.GND-D1, CN25.GND-D2, CN27.1, CN28.3, CN29.1, R17.1, U12.1, U13.1, U14.15
I2C_SCL: CN6.4, CN7.4, CN8.4, CN9.4, U2.17
I2C_SCL1: CN12.4, CN14.4, U5.17
I2C_SCL2: CN17.4, CN19.4, U8.17
I2C_SCL3: CN22.4, CN24.4, U11.17
I2C_SCL4: CN27.4, CN29.4, U14.17
I2C_SDA: CN6.5, CN7.5, CN8.5, CN9.5, U2.18
I2C_SDA1: CN12.5, CN14.5, U5.18
I2C_SDA2: CN17.5, CN19.5, U8.18
I2C_SDA3: CN22.5, CN24.5, U11.18
I2C_SDA4: CN27.5, CN29.5, U14.18
unnamed: R1.1, R2.2, U1.3
unnamed: LED1.C, R4.2
unnamed: LED1.A, U2.7
unnamed: C1.2, R3.1, U2.6
unnamed: R5.2, U2.1
unnamed: R3.2, U1.1, U1.2
unnamed: CN4.1, SW1.5
unnamed: CN3.1, SW1.2
unnamed: CN11.2, U3.5, U3.6, U3.7, U3.8
unnamed: CN11.1, U4.5, U4.6, U4.7, U4.8
unnamed: R6.1, U3.2, U3.4
unnamed: R7.2, U4.2, U4.4
unnamed: R8.2, U5.1
unnamed: R7.1, U5.10
unnamed: R6.2, U5.9
unnamed: CN13.1, U5.8
unnamed: CN16.2, U6.5, U6.6, U6.7, U6.8
unnamed: CN16.1, U7.5, U7.6, U7.7, U7.8
unnamed: R9.1, U6.2, U6.4
unnamed: R10.2, U7.2, U7.4
unnamed: R11.2, U8.1
unnamed: R10.1, U8.10
unnamed: R9.2, U8.9
unnamed: CN18.1, U8.8
unnamed: CN21.2, U9.5, U9.6, U9.7, U9.8
unnamed: CN21.1, U10.5, U10.6, U10.7, U10.8
unnamed: R12.1, U9.2, U9.4
unnamed: R13.2, U10.2, U10.4
unnamed: R14.2, U11.1
unnamed: R13.1, U11.10
unnamed: R12.2, U11.9
unnamed: CN23.1, U11.8
unnamed: CN26.2, U12.5, U12.6, U12.7, U12.8
unnamed: CN26.1, U13.5, U13.6, U13.7, U13.8
unnamed: R15.1, U12.2, U12.4
unnamed: R16.2, U13.2, U13.4
unnamed: R17.2, U14.1
unnamed: R16.1, U14.10
unnamed: R15.2, U14.9
unnamed: CN28.1, U14.8
NRST: CN1.12, CN2.NRST
NRST1: CN0.NRST, U2.4
NRST2: CN10.NRST, U5.4
NRST3: CN15.NRST, U8.4
NRST4: CN20.NRST, U11.4
NRST5: CN25.NRST, U14.4
SPI_CE: CN5.3, U2.10
SPI_CSN: CN5.4, U2.9
SPI_IRQ: CN5.8, U2.14
SPI_MISO: CN5.7, U2.12
SPI_MOSI: CN5.6, U2.13
SPI_SCK: CN5.5, U2.11
SWCLK: CN1.06, CN2.CLK
SWCLK1: CN0.CLK, U2.20
SWCLK2: CN10.CLK, U5.20
SWCLK3: CN15.CLK, U8.20
SWCLK4: CN20.CLK, U11.20
SWCLK5: CN25.CLK, U14.20
SWDIO: CN1.04, CN2.DIO
SWDIO1: CN0.DIO, U2.19
SWDIO2: CN10.DIO, U5.19
SWDIO3: CN15.DIO, U8.19
SWDIO4: CN20.DIO, U11.19
SWDIO5: CN25.DIO, U14.19
T_VCC: CN1.03, CN2.VCC
VCC: CN0.VCC, CN5.2, CN6.2, CN7.2, CN8.2, CN9.2, R4.1, SW1.1, U1.8, U2.5, U2.16
VCC1: CN10.VCC, CN12.2, CN14.2, U5.5, U5.16
VCC2: CN15.VCC, CN17.2, CN19.2, U8.5, U8.16
VCC3: CN20.VCC, CN22.2, CN24.2, U11.5, U11.16
VCC4: CN25.VCC, CN27.2, CN29.2, U14.5, U14.16

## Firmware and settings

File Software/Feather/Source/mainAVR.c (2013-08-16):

#include "mainAVR.h"
#include <avr/io.h>
#include <avr/interrupt.h>

volatile unsigned char position = 40;	//7...40

volatile uint8_t s_motorA = 0;
volatile uint8_t s_motorB = 0;

volatile uint8_t s_counter = 0;
char s_spiState = 0;

#define MOTOR_PIN_A PB3
#define MOTOR_PIN_B	PB4

int main(void)
{
	Init();
    while(1)
    {
		;
    }
}


void UpdateCounter(uint8_t additional)
{
	uint8_t dt = 0xff - s_counter;
	if(dt < additional)
	{
		s_counter = additional - dt;
	}
	else
	{
		s_counter += additional;
	}
}


void Init()
{
	// Default frequency is 8.0 MHz divided by 1
	// System frequency = 8.0 MHz
	
	/* === Configure prescale here ===	*/
	uint8_t clkpr = (0 & CLKPS0)|
					(0 & CLKPS1)|
					(0 & CLKPS2)|
					(0 & CLKPS3);
	WRITE_REG(CLKPR, CLKPCE);
	WRITE_REG(CLKPR, clkpr);
	
	
	
	/* === Configure timer here === */	
	// Stop timers
	SET_BIT(GTCCR, TSM);
	{
		SET_BIT(TCCR0B, CS00); // Set source Fcpu/64
		SET_BIT(TCCR0B, CS01);
		
		SET_BIT(TIMSK, OCIE0A); // Interrupt on compare match A
		SET_BIT(TIMSK, OCIE0B); // Interrupt on compare match B
		SET_BIT(TIMSK, TOV0); // Interrupt on timer overflow
			
		WRITE_REG(OCR0A, s_motorA);
		WRITE_REG(OCR0B, s_motorB);
	}
	// start timers
	CLEAR_BIT(GTCCR, TSM);	
	
	// The rising edge of INT0 generates an interrupt request.
	SET_BIT(MCUCR, ISC00);
	SET_BIT(MCUCR, ISC01);
	SET_BIT(GIMSK, INT0); // Enable INT0 interrupt
	
	SET_BIT(USICR, USIWM0);
	SET_BIT(USICR, USICS1);
	
	SET_BIT(PORTB, MOTOR_PIN_A);
	SET_BIT(PORTB, MOTOR_PIN_B);
	SET_BIT(DDRB, MOTOR_PIN_A);
	SET_BIT(DDRB, MOTOR_PIN_B);
	
	sei();
}

// === SPI ===
ISR(INT0_vect)
{
	ReadSpi();
}

void ReadSpi()
{
	if(s_spiState == 0)
	{
		if((USIDR) == PRIMARY_LETTER)
		{
			++s_spiState;
		}
	}
	else if(s_spiState < 9)
	{
		++s_spiState;
	}
	else if(s_spiState == 9)
	{
		if(USIDR == SECONDARY_LETTER)
		{
			++s_spiState;
		}
		else
		{
			s_spiState = 0;
		}
	}
	else if(s_spiState < 18)
	{
		++s_spiState;
	}
	else if(s_spiState == 18)
	{
		SetMotorSpeedSigned(USIDR);
		++s_spiState;
	}
	else if(s_spiState < 27)
	{
		++s_spiState;
	}
	else if(s_spiState == 27)
	{		
		SetServoPosition(USIDR);
		s_spiState = 0;
	}
}

// === Servo controls ===
void SetServoPosition(unsigned char position)
{
	
}

// === DC motor controls ===
// -128 - max CCW, 0 - stop, 127 - max CW
void SetMotorSpeedSigned(signed char speed)
{
	cli();
	if(speed > 0)
	{
		uint8_t newSpeed = speed;
		s_motorA = newSpeed << 1;
		s_motorB = 0;
	}
	else
	{
		uint8_t newSpeed = -speed;
		s_motorA = 0;
		s_motorB = newSpeed << 1;
	}
	sei();
}

// 0 - max CCW, 127 - stop, 255 - max CW
void SetMotorSpeedUnsigned(unsigned char speed)
{
	cli();
	if(speed > 127)
	{
		uint8_t newSpeed = speed - 127;
		s_motorA = newSpeed << 1;
		s_motorB = 0;		
	}
	else
	{
		uint8_t newSpeed = 127 - speed;
		s_motorA = 0;
		s_motorB = newSpeed << 1;
	}
	sei();
}

ISR(TIM0_COMPA_vect)
{
	CLEAR_BIT(PORTB, MOTOR_PIN_A);
}
ISR(TIM0_COMPB_vect)
{
	CLEAR_BIT(PORTB, MOTOR_PIN_B);
}

ISR(TIM0_OVF_vect)
{
	if(s_motorA != 0)
		SET_BIT(PORTB, MOTOR_PIN_A);
	if(s_motorB != 0)
		SET_BIT(PORTB, MOTOR_PIN_B);
	
	WRITE_REG(OCR0A, s_motorA);
	WRITE_REG(OCR0B, s_motorB);
}

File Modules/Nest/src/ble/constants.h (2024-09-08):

#pragma once

/**
 * Advertising Data Structures
 * https://www.bluetooth.com/specifications/assigned-numbers/generic-access-profile/
 */
enum AdvData {
	EAdvData_Flags =                      0x01, // Flags
	EAdvData_Services16 =                 0x02, // Incomplete List of 16-bit Service Class UUIDs
	EAdvData_Services16Complete =         0x03, // Complete List of 16-bit Service Class UUIDs
	EAdvData_Services32 =                 0x04, // Incomplete List of 32-bit Service Class UUIDs
	EAdvData_Services32Complete =         0x05, // Complete List of 32-bit Service Class UUIDs
	EAdvData_Services128 =                0x06, // Incomplete List of 128-bit Service Class UUIDs
	EAdvData_Services128Complete =        0x07, // Complete List of 128-bit Service Class UUIDs
	EAdvData_Name =                       0x08, // Shortened Local Name
	EAdvData_NameComplete =               0x09, // Complete Local Name
	EAdvData_TxPower =                    0x0A, // Tx Power Level
	EAdvData_Class =                      0x0D, // Class of Device
	EAdvData_PairingHashC =               0x0E, // Simple Pairing Hash C
	EAdvData_PairingHashC192 =            0x0E, // Simple Pairing Hash C-192
	EAdvData_PairingHashR =               0x0F, // Simple Pairing Randomizer R
	EAdvData_PairingHashR192 =            0x0F, // Simple Pairing Randomizer R-192
	EAdvData_DeviceId =                   0x10, // Device ID
	EAdvData_SecTkValue =                 0x10, // Security Manager TK Value
	EAdvData_SecOutOfBandFlags =          0x11, // Security Manager Out of Band Flags
	EAdvData_ConnectionIntervalRange =    0x12, // Slave Connection Interval Range
	EAdvData_Services16Solicitation =     0x14, // List of 16-bit Service Solicitation UUIDs
	EAdvData_Services128Solicitation =    0x15, // List of 128-bit Service Solicitation UUIDs
	EAdvData_ServiceData =                0x16, // Service Data
	EAdvData_PublicTargetAddr =           0x17, // Public Target Address
	EAdvData_RandomTargetAddr =           0x18, // Random Target Address
	EAdvData_Appearance =                 0x19, // Appearance
	EAdvData_AdvInterval =                0x1A, // Advertising Interval
	EAdvData_LeDeviceAddr =               0x1B, // LE Bluetooth Device Address	
	EAdvData_LeRole =                     0x1C, // LE Role
	EAdvData_PairingC256 =                0x1D, // Simple Pairing Hash C-256
	EAdvData_PairingR256 =                0x1E, // Simple Pairing Randomizer R-256
	EAdvData_Services32Solicitation =     0x1F, // List of 32-bit Service Solicitation UUIDs
	EAdvData_ServiceData32 =              0x20, // Service Data - 32-bit UUID
	EAdvData_ServiceData128 =             0x21, // Service Data - 128-bit UUID
	EAdvData_LeSecConConfirmationVal =    0x22, // LE Secure Connections Confirmation Value
	EAdvData_LeSecConRandomVal =          0x23, // LE Secure Connections Random Value
	EAdvData_Uri =                        0x24, // URI
	EAdvData_IndoorPositioning =          0x25, // Indoor Positioning
	EAdvData_TransportDiscoveryData =     0x26, // Transport Discovery Data
	EAdvData_LeSupportedFeatures =        0x27, // LE Supported Features
	EAdvData_ChannelMapUpdateIndication = 0x28, // Channel Map Update Indication
	EAdvData_PbAdv =                      0x29, // PB-ADV
	EAdvData_MeshMessage =                0x2A, // Mesh Message
	EAdvData_MeshBeacon =                 0x2B, // Mesh Beacon
	EAdvData_BigInfo =                    0x2C, // BIGInfo
	EAdvData_BroadcastCode =              0x2D, // Broadcast_Code
	EAdvData_InformationData3d =          0x3D, // 3D Information Data
	EAdvData_ManufacturerSpecificData =   0xFF, // Manufacturer Specific Data
};
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

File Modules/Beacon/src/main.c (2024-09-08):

#include "main.h"
#include "program.h"
#include "stm32l0xx_hal.h"
#include "printf.h"

RTC_HandleTypeDef s_rtc;
UART_HandleTypeDef s_uart2;
SPI_HandleTypeDef s_spi1;
CRC_HandleTypeDef s_crc;

CRC_HandleTypeDef* GetCrc() { return &s_crc; }
SPI_HandleTypeDef* GetSpi() { return &s_spi1; }
UART_HandleTypeDef* getUart() { return &s_uart2; }

void Error_Handler() {
	void __blocking_handler();
	__blocking_handler();
}
static void RTC_Init();
static void Clock_Init();
static void GPIO_Init();
static void USART2_UART_Init();
static void SPI1_Init();
static void CRC_Init();

int main(void) {
#ifdef _DEBUG
	volatile uint8_t stop = 0;
	while (stop);
#endif

	HAL_Init();
	Clock_Init();
	RTC_Init();
	GPIO_Init();
	USART2_UART_Init();
	SPI1_Init();
	CRC_Init();

	setup();

	while(1) {
		poll();
	}
}

static void Clock_Init() {
	// Configure the main internal regulator output voltage
	__HAL_PWR_VOLTAGESCALING_CONFIG(PWR_REGULATOR_VOLTAGE_SCALE1);
	
	// Initializes the CPU, AHB and APB busses clocks 
	RCC_OscInitTypeDef rccOsc = {0};
	rccOsc.OscillatorType = RCC_OSCILLATORTYPE_HSI|RCC_OSCILLATORTYPE_LSI;
	rccOsc.HSIState = RCC_HSI_ON;
	rccOsc.HSICalibrationValue = RCC_HSICALIBRATION_DEFAULT;
	rccOsc.LSIState = RCC_LSI_ON;
	rccOsc.PLL.PLLState = RCC_PLL_NONE;
	if (HAL_RCC_OscConfig(&rccOsc) != HAL_OK) {
		Error_Handler();
	}

	// Initializes the CPU, AHB and APB busses clocks
	RCC_ClkInitTypeDef rccClk = {0};
	rccClk.ClockType = RCC_CLOCKTYPE_HCLK|RCC_CLOCKTYPE_SYSCLK|RCC_CLOCKTYPE_PCLK1|RCC_CLOCKTYPE_PCLK2;
	rccClk.SYSCLKSource = RCC_SYSCLKSOURCE_HSI;
	rccClk.AHBCLKDivider = RCC_SYSCLK_DIV1;
	rccClk.APB1CLKDivider = RCC_HCLK_DIV1;
	rccClk.APB2CLKDivider = RCC_HCLK_DIV1;
	if (HAL_RCC_ClockConfig(&rccClk, FLASH_LATENCY_0) != HAL_OK) {
		Error_Handler();
	}

	RCC_PeriphCLKInitTypeDef periphClck = {0};
	periphClck.PeriphClockSelection = RCC_PERIPHCLK_USART2|RCC_PERIPHCLK_RTC;
	periphClck.Usart2ClockSelection = RCC_USART2CLKSOURCE_PCLK1;
	periphClck.RTCClockSelection = RCC_RTCCLKSOURCE_LSI;
	if (HAL_RCCEx_PeriphCLKConfig(&periphClck) != HAL_OK) {
		Error_Handler();
	}
}

static void RTC_Init() {
	// Initialize RTC Only
	s_rtc.Instance = RTC;
	s_rtc.Init.HourFormat = RTC_HOURFORMAT_24;
	s_rtc.Init.AsynchPrediv = 127;
	s_rtc.Init.SynchPrediv = 255;
	s_rtc.Init.OutPut = RTC_OUTPUT_DISABLE;
	s_rtc.Init.OutPutRemap = RTC_OUTPUT_REMAP_NONE;
	s_rtc.Init.OutPutPolarity = RTC_OUTPUT_POLARITY_HIGH;
	s_rtc.Init.OutPutType = RTC_OUTPUT_TYPE_OPENDRAIN;
	if (HAL_RTC_Init(&s_rtc) != HAL_OK) {
		Error_Handler();
	}

	// Initialize RTC and set the Time and Date
	RTC_TimeTypeDef rtcTime = {0};
	rtcTime.Hours = 0;
	rtcTime.Minutes = 0;
	rtcTime.Seconds = 0;
	rtcTime.DayLightSaving = RTC_DAYLIGHTSAVING_NONE;
	rtcTime.StoreOperation = RTC_STOREOPERATION_RESET;
	if (HAL_RTC_SetTime(&s_rtc, &rtcTime, RTC_FORMAT_BIN) != HAL_OK) {
		Error_Handler();
	}

	RTC_DateTypeDef rtcDate = {0};
	rtcDate.WeekDay = RTC_WEEKDAY_MONDAY;
	rtcDate.Month = RTC_MONTH_JANUARY;
	rtcDate.Date = 1;
	rtcDate.Year = 0;
	if (HAL_RTC_SetDate(&s_rtc, &rtcDate, RTC_FORMAT_BIN) != HAL_OK) {
		Error_Handler();
	}

	// Enable the Alarm A
	RTC_AlarmTypeDef rtcAlarm = {0};
	rtcAlarm.AlarmTime.Hours = 0;
	rtcAlarm.AlarmTime.Minutes = 0;
	rtcAlarm.AlarmTime.Seconds = 0;
	rtcAlarm.AlarmTime.SubSeconds = 0;
	rtcAlarm.AlarmTime.DayLightSaving = RTC_DAYLIGHTSAVING_NONE;
	rtcAlarm.AlarmTime.StoreOperation = RTC_STOREOPERATION_RESET;
	rtcAlarm.AlarmMask = RTC_ALARMMASK_ALL;
	rtcAlarm.AlarmSubSecondMask = RTC_ALARMSUBSECONDMASK_ALL;
	rtcAlarm.AlarmDateWeekDaySel = RTC_ALARMDATEWEEKDAYSEL_DATE;
	rtcAlarm.AlarmDateWeekDay = 1;
	rtcAlarm.Alarm = RTC_ALARM_A;
	if (HAL_RTC_SetAlarm_IT(&s_rtc, &rtcAlarm, RTC_FORMAT_BIN) != HAL_OK) {
		Error_Handler();
	}
}

static void GPIO_Init() {
	GPIO_InitTypeDef port = {0};

	__HAL_RCC_GPIOA_CLK_ENABLE();
	__HAL_RCC_GPIOB_CLK_ENABLE();

	/*Configure GPIO pin : PA1 */
	HAL_GPIO_WritePin(GPIOA, GPIO_PIN_1, GPIO_PIN_RESET);
	port.Pin = GPIO_PIN_1;
	port.Mode = GPIO_MODE_OUTPUT_PP;
	port.Pull = GPIO_NOPULL;
	port.Speed = GPIO_SPEED_FREQ_LOW;
	HAL_GPIO_Init(GPIOA, &port);	

	/*Configure GPIO pin : PB1 */
	port.Pin = GPIO_PIN_1;
	port.Mode = GPIO_MODE_IT_FALLING;
	port.Pull = GPIO_NOPULL;
	HAL_GPIO_Init(GPIOB, &port);

	/* EXTI interrupt init*/
	HAL_NVIC_SetPriority(EXTI0_1_IRQn, 0, 0);
	HAL_NVIC_EnableIRQ(EXTI0_1_IRQn);
}

static void USART2_UART_Init() {
	s_uart2.Instance = USART2;
	s_uart2.Init.BaudRate = 115200;
	s_uart2.Init.WordLength = UART_WORDLENGTH_8B;
	s_uart2.Init.StopBits = UART_STOPBITS_1;
	s_uart2.Init.Parity = UART_PARITY_NONE;
	s_uart2.Init.Mode = UART_MODE_TX_RX;
	s_uart2.Init.HwFlowCtl = UART_HWCONTROL_NONE;
	s_uart2.Init.OverSampling = UART_OVERSAMPLING_16;
	s_uart2.Init.OneBitSampling = UART_ONE_BIT_SAMPLE_DISABLE;
	s_uart2.AdvancedInit.AdvFeatureInit = UART_ADVFEATURE_NO_INIT;
	if (HAL_UART_Init(&s_uart2) != HAL_OK) {
		Error_Handler();
	}
	HAL_NVIC_SetPriority(USART2_IRQn, 0, 0);
	HAL_NVIC_EnableIRQ(USART2_IRQn);
}

static void SPI1_Init(void) {
	s_spi1.Instance = SPI1;
	s_spi1.Init.Mode = SPI_MODE_MASTER;
	s_spi1.Init.Direction = SPI_DIRECTION_2LINES;
	s_spi1.Init.DataSize = SPI_DATASIZE_8BIT;
	s_spi1.Init.CLKPolarity = SPI_POLARITY_LOW;
	s_spi1.Init.CLKPhase = SPI_PHASE_1EDGE;
	s_spi1.Init.NSS = SPI_NSS_SOFT;
	s_spi1.Init.BaudRatePrescaler = SPI_BAUDRATEPRESCALER_2;
	s_spi1.Init.FirstBit = SPI_FIRSTBIT_MSB;
	s_spi1.Init.TIMode = SPI_TIMODE_DISABLE;
	s_spi1.Init.CRCCalculation = SPI_CRCCALCULATION_DISABLE;
	s_spi1.Init.CRCPolynomial = 7;
	if (HAL_SPI_Init(&s_spi1) != HAL_OK) {
		Error_Handler();
	}
}

static void CRC_Init() {
	s_crc.Instance = CRC;
	s_crc.Init.DefaultPolynomialUse = DEFAULT_POLYNOMIAL_DISABLE;
	s_crc.Init.DefaultInitValueUse = DEFAULT_INIT_VALUE_DISABLE;
	s_crc.Init.GeneratingPolynomial = 7;
	s_crc.Init.CRCLength = CRC_POLYLENGTH_8B;
	s_crc.Init.InitValue = 0;
	s_crc.Init.InputDataInversionMode = CRC_INPUTDATA_INVERSION_NONE;
	s_crc.Init.OutputDataInversionMode = CRC_OUTPUTDATA_INVERSION_DISABLE;
	s_crc.InputDataFormat = CRC_INPUTDATA_FORMAT_BYTES;
	if (HAL_CRC_Init(&s_crc) != HAL_OK) {
		Error_Handler();
	}
}

uint8_t PZ_crc(uint8_t const* data, uint8_t size) {
	return HAL_CRC_Calculate(GetCrc(), (uint32_t*)data, size);
}

void _putchar(char character) {
	HAL_UART_Transmit(&s_uart2, (uint8_t*) &character, 1, HAL_MAX_DELAY);
}

void SysTick_Handler() {
	HAL_IncTick();
}

void RTC_IRQHandler() {
	onTimer();
	HAL_RTC_AlarmIRQHandler(&s_rtc);
}

void EXTI0_1_IRQHandler() {
	onExtIrq();
	HAL_GPIO_EXTI_IRQHandler(GPIO_PIN_1);
}

void USART2_IRQHandler() {
	HAL_UART_IRQHandler(&s_uart2);
	onUart();
}

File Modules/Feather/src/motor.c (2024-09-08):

#include "motor.h"
#include "main.h"
#include "dynamicvalues.h"
#include "configurablevalues.h"
#include "stm32l011xx.h"

// The Feather version 1.0 schematic does not take advantage of the hardware
// pwm channels. Thus the ports are triggered in software.
// The HAL takes t0o much time to wrap all the calls so this file does
// not use it for performance reasons.

static const uint16_t s_maxMotorTimerValue = 500; // Corresponds to 500 us

static void _setMotor(int8_t value);
static int32_t motorToTimerValue(int8_t value);

void motorInit() {
	_setMotor(getMotor());

	TIM2->ARR = s_maxMotorTimerValue;
	// Enable interrupts for compare 1, compare 2, and update
	TIM2->DIER |= TIM_DIER_CC1IE | TIM_DIER_CC2IE | TIM_DIER_UIE;
	TIM2->CR1 |= TIM_CR1_CEN;
}

static int32_t motorToTimerValue(int8_t value) {
	if (getMotorCalMode() == 0) {
		if (value < 0) {
			// value is in range -128 ... -1
			const int32_t range = -value; // 128 ... 1

			const int32_t motorRange = (255 - (128 + getMotorCal1())) * s_maxMotorTimerValue / 255;
			
			const int32_t motorValue = range * motorRange / 128;
			return -motorValue;
		}
		else if (value > 0) {
			// value is in range 1 ... 127
			const int32_t range = value; // 1 ... 127

			const int32_t motorRange = (128 + getMotorCal2()) * s_maxMotorTimerValue / 255;

			const int32_t motorValue = range * motorRange / 127;
			//const int32_t minimal = getMotorCal2();
			return motorValue;
		}
		else {
			return 0;
		}
	}
	else if (getMotorCalMode() == 1) {
		// value is in range -128 ... 127
		const int32_t range = 255 - (128 + value); // 255 ... 0
		const int32_t motorValue = range * s_maxMotorTimerValue / 255;
		return -motorValue;
	}
	else if (getMotorCalMode() == 2) {
		// value is in range -128 ... 127
		const int32_t range = 128 + value; // 0 ... 255
		const int32_t motorValue = range * s_maxMotorTimerValue / 255;
		return motorValue;
	}
	return 0;
}

static void _setMotor(int8_t value) {
	const int32_t tv = motorToTimerValue(value);
	if (tv > 0) {
		TIM2->CCR1 = (uint16_t)tv;
		TIM2->CCR2 = 0;
	}
	else if (tv < 0) {
		TIM2->CCR1 = 0;
		TIM2->CCR2 = (uint16_t)(-tv);
	}
	else {
		TIM2->CCR1 = 0;
		TIM2->CCR2 = 0;
	}
}

void DvOnMotorChanged(int8_t value) {
	_setMotor(value);
}

void DvOnMotorCalModeChanged(uint8_t value) {
	switch (value) {
		case 0: // Normal mode
			setMotor(getMotorDef());
			break;
		case 1: // Calibrating minimal value
			setMotor(getMotorCal1());
			break;
		case 2: // Calibrating maximal value
			setMotor(getMotorCal2());
			break;
		default:
			break;
	}
	_setMotor(getMotor());
}

void CvOnMotorCal1Changed(int8_t value) {
	(void)value;
	_setMotor(getMotor());
}

void CvOnMotorCal2Changed(int8_t value) {
	(void)value;
	_setMotor(getMotor());
}

void TIM2_IRQHandler() {
	// Compare 1 match
	if (TIM2->SR & TIM_SR_CC1IF) {
		TIM2->SR = ~TIM_SR_CC1IF; // Clear interrupt flag
		if (TIM2->CCR1 != TIM2->ARR) {
			GPIOA->BRR = GPIO_PIN_3;
		}
	}
	// Compare 2 match
	if (TIM2->SR & TIM_SR_CC2IF) {
		TIM2->SR = ~TIM_SR_CC2IF; // Clear interrupt flag
		if (TIM2->CCR2 != TIM2->ARR) {
			GPIOA->BRR = GPIO_PIN_4;
		}
	}
	// Timer update
	if (TIM2->SR & TIM_SR_UIF) {
		TIM2->SR = ~TIM_SR_UIF; // Clear interrupt flag
		GPIOA->BSRR = ((TIM2->CCR1 != 0) * GPIO_PIN_3) | ((TIM2->CCR2 != 0) * GPIO_PIN_4);
	}
}

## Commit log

2013-08-10 Initial commit of all I have
    [baloon.dwg, calculations.xlsx, parts.dwg]
2013-08-11 Added schematics and circuits empty projects
    [Feather.brd, Feather.sch, Nest.brd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]
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2013-08-13 Created models of servo and DC motor
    [baloon.dwg]
2013-08-14 Added schematics lib for transistor pair irf7105 Added schematics for H-bridge
    [Nest.brd, Nest.sch]
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2013-08-15 Added new project for "keel" part of the zeppelin Added lib for soft SPI
2013-08-16 Fixed stream buffer. Now it works, but still needs a fix. Configured Keel timer. Modified Keel Axon.
    [main.c, main.h]
2013-08-16 Fixed Feather SPI receiver
    [mainAVR.c]
2013-08-16 Updated data header and device identification method Incorrect behavior of DC motor when received 0. To fix.
    [mainAVR.c]
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2013-08-19 Added schematics for Feather
    [Feather.sch]
2013-08-19 Created pcb for Feather
    [Feather.brd]
2013-08-19 Feather board routed
    [Feather.brd, Feather.sch]
2013-08-19 Rounded corners to look nice and pass DRC
    [Feather.brd]
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2013-08-24 Moved servo and dc motor from dirajuble
    [parts.dwg]
2013-08-24 Scaled ballon
    [baloon.dwg]
2013-08-24 Set balloon scale
    [calculations.xlsx]
2013-08-24 added wrap for balloon
    [wrap.dwg]
2013-08-24 Added flaps
    [wrap.dwg]
2013-08-24 more flaps added layout and dimensions
    [wrap.dwg]
2013-08-25 Changed mcu, redrawn scheme, redrawn pcb
    [Feather.brd, Feather.sch]
2013-08-25 Created Keel eagle project
    [Keel.brd, Keel.sch]
2013-08-25 Created PCB for Keel
    [Keel.brd, Keel.sch]
2013-08-25 Simplify PCB by remapping pins
    [Keel.brd, Keel.sch]
2013-08-25 Updated PCB
    [Keel.brd]
2013-08-25 Basic elements for Nest scheme
    [Nest.brd, Nest.sch]
2013-08-25 Added Feather blueprints
    [Feather.dwg]
2013-08-25 Added more details
    [Feather.dwg]
2013-08-25 Added separate file for Feather motor cover
    [Feather_Motor_Cover.dwg]
2013-08-26 Converted curves to polylines
    [Feather.dwg, Feather_Motor_Cover.dwg]
2013-08-26 Converted to curves
    [Feather_Motor_Cover.dwg]
2013-08-26 More curves
    [Feather_Motor_Cover.dwg]
2013-08-26 Created surface
    [Feather_Motor_Cover.dwg]
2013-08-26 Added servo cover
    [Feather_Motor_Cover.dwg]
2013-08-26 Prolonged servo cover
    [Feather_Motor_Cover.dwg]
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2013-08-27 Updated wrap for balloon 4.4[m] x 1.2[m] and 3[m] x 1.5[m]
    [wrap.dwg]
2013-08-29 Fixed SPI word size
    [main.c]
2013-08-30 Added servo configurations Fixed servo pins Added servo controller Cleaned up unused code
    [main.c, main.h]
2013-08-30 Split CPU power and motor power Updated PCB
    [Feather.brd, Feather.sch]
2013-08-30 Changed MCU package
    [Feather.brd, Feather.sch]
2013-08-30 Updated Keel communication with transceiver Fixed TransmitPool
    [main.c]
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2013-09-04 Updated wrap
    [wrap.dwg]
2013-09-05 Fixed compilation errors Added test project
    [main.c]
2013-09-06 Fixed error when compiling without optimization
    [main.c]
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2013-09-06 Fixed multiple stick calibration
    [main.c]
2013-09-07 Added Nest mode icons variants
    [Protype.dwg]
2013-09-12 Added 3draft added 3draft renders added stck model added icon renders
    [3draft.dwg, Protype.dwg, mode_icons.dwg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]
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2013-09-12 Added stick references Added Nest pcb dimensions Added 3draft of smaller size
    [3draft.dwg, Protype.dwg, stick.dwg]
2013-09-13 Added stick footprint Drawn Nest PCB dimensions Added sticks on board and scheme
    [Nest.brd, Nest.sch]
2013-09-14 Added pinhead library with smaller pads Changed Keel MCU package Added dimensions to Keel Updated dimension in Feather project
    [Feather.brd, Keel.brd, Keel.sch]
2013-09-14 Added outfiles for printing Feather and Keel PCBs
    [Feather.brd, Keel.brd]
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2013-09-14 Added Analog power filter to Nest scheme Added MCU configuration module for Nest
    [Nest.brd, Nest.sch]
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2013-09-15 Nest. Fixed data sending via Axon Nest. Fixed EEPROM data loading
    [main.c]
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2013-09-18 Fixed CPU prescale. How did it even worked before? Need to check timing now.
    [main.c]
2013-09-20 Increased pads size for Keel and Feather PCBs
    [Feather.brd, Feather.sch, Keel.brd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]
2013-09-20 Nest scheme. Added RF module. Routed bottom layer with ground and power buses
    [Nest.brd, Nest.sch]
2013-09-21 Added connector project for firmware uploading
    [Connector.brd, Connector.sch]
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2013-09-22 Keel scheme. Fixed terrible error in circuit
    [Keel.brd, Keel.sch]
2013-09-22 Keel scheme. Routed PCB for fixed circuit Nest scheme. Added elements and routed a piece of PCB
    [Keel.brd, Keel.sch, Nest.brd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]
2013-09-26 Added new blueprint for 3draft with full scale Renamed old files to fix mistakes
    [3draft.dwg]
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2014-03-19 Some changes. sorry
    [stick.dwg]
2014-08-15 - Updated calculations
    [calculations.xlsx]
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2014-08-19 * Fixed feather bugs - Feather debugging functions added ! Not working feather - Updated upload scripts - Updated calculations for selected fabrics
    [calculations.xlsx]
2014-08-21 - [Feather] Updated script and fixed USI byte overflow
    [main.c]
2014-08-21 * Fixed Feather - Removed debug calls
    [main.c]
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2016-06-11 Added mounts for feather components. Added feather models for printing. Refactored feather software.
    [Feather_Motor_Cover.dwg, Feather_cover2_print.stl, Feather_cover_print.stl]
2016-06-11 Converted assembled balloon to blender format. Added render of assembled balloon
    [assembled_balloon.blend]
2016-06-11 Translated calculations
    [calculations.xlsx]
2016-06-18 Added tools for programmer on mac. Added libraries with connectors and wireless module. Updated Keel schema and PCB. Added DRC.
    [Keel.brd, Keel.sch]
2016-06-19 Software. Fixed asm nop macro. Keel removed unused code, updated config and logic for new controller attiny2313
    [main.c]
2016-06-19 Ignored temporary and generated files. Keel Software. Removed redundant files of SPI module. Cleaned up code and fixed bugs.
    [main.c, main.h]
2016-06-21 Software. Fixed util functions. Keel. Added emulation mode
    [main.c, main.h]
2016-07-14 Updated dimension of the motor GPS-7
    [Feather.dwg]
2016-08-03 Added 3d models for parts
    [feather_motor.stl, feather_motor_cover.stl, feather_screw.stl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]
2020-01-05 Addeed beacon schematics
    [beacon.brd, beacon.sch]
2020-01-06 Working beacon project
    [beacon.brd, beacon.sch]
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2020-01-17 Fixed cmake Added ducktape breakpoint at the start
    [main.h]
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2020-01-18 Enabled Os optimization Added code to send data Fixed nrf24 lib printing
    [hal_msp.c, main.c, main.h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]
2020-01-18 Fixed SPI intialization code. Working transmitter and receiver
    [main.c, main.h, nrf24_hw_conf.h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]
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2020-01-25 Added missing functions to feather CV and DV
    [configurablevalues.c, dynamicvalues.c]
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2020-01-29 Moved eagle libraries and project
    [keel.brd, keel.sch]
2020-01-31 Traced keel
    [keel.brd, keel.sch]
2020-01-31 Traced feather
    [feather.brd, feather.sch]
2020-01-31 Traced probe
    [probe.brd, probe.sch]
2020-02-01 Updated libraries Added DRU Added group board variants
    [group-bare.brd, group.brd]
2020-02-01 Updated layers
    [feather.brd, group-bare.brd, group.brd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]
2020-02-03 Updated milling and border layers
    [group.brd]
2020-02-03 downgraded version eagle version to 9.2.2
    [group.brd]
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2020-02-06 Fixed DMA buffer overrun
    [main.c, program.c]
2020-02-07 [Feather] Added servo calibration mode Updated protocol documentation Fixed I2C address change
    [configurablevalues.c, dynamicvalues.c, main.c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]
2020-02-07 [Keel] Fixed inifnite loop on I2C error
    [dendrite.c]
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2020-02-08 Removed old circuits and schematics
    [Connector.brd, Connector.sch, Feather.brd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]
2020-02-08 Removed obsolete files
    [3draft.dwg]
2020-02-15 Fixed initialization of nrf24 Set speed to 2Mbps Added commands for beacon
    [program.c]
2020-02-15 Updated board to version 1.0.1 Fixed switch position Replaced connectors with horizontal versions Changed voltage divider from 0.5 to 0.164 Fixed LED orientation
    [keel.brd, keel.sch]
2020-02-16 Fixed schematic issues from version 1.0.0 Added datasheets for new components
    [feather.brd, feather.sch, keel.brd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]
2020-02-16 Replaced regulator with LDO
    [keel.brd, keel.sch]
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2020-02-27 Replaced app ble with bleapp
    [bleapp.c, wpanapp.c]

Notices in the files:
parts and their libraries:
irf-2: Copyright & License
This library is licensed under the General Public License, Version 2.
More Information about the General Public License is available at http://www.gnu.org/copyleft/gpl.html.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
